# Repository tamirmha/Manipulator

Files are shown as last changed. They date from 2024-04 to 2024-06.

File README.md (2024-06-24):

# Homemade Manipulator Arm Project

Welcome to the Homemade Manipulator Arm project repository! This project features a DIY robotic arm with 6 degrees of freedom (6DoF) and a gripper. The arm is controlled using 4 MG1501 servos and 3 SG90 servos. The project includes SolidWorks 3D part designs, electrical schemas created with EasyEDA, and the ESP code for controlling the arm.
Use [PlatformIO](https://platformio.org/) in Visual Studio Code (VSCode) to manage and upload the code to the ESP microcontroller.

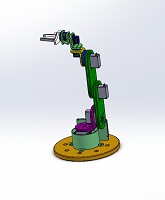
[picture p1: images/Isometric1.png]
Isometric View

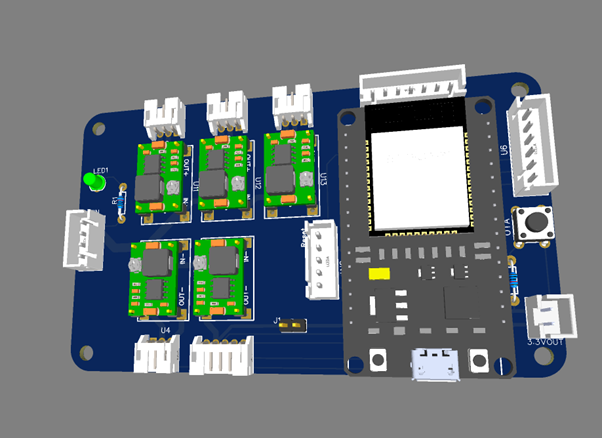
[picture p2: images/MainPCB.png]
Main PCB Board 3D

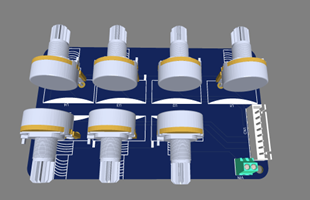
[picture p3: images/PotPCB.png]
Potentiometer PCB Board 3D

## Contents

- [Description](#description)
- [Components](#components)
- [Folder Structure](#folder-structure)
- [Usage](#usage)
- [Credits](#credits)
- [Sponsors](#sponsors)
- [License](#license)

## Description

This project is a homemade manipulator arm designed for educational purposes and hobbyist robotics enthusiasts. The arm is built using 3D-printed parts designed in SolidWorks and controlled using ESP32 microcontroller boards. The control methods include Bluetooth Low Energy (BLE) using the [RemoteXY](https://remotexy.com/) library or manual control using encoders (potentiometers).

The kinematics of the manipulator are represented using the Denavit-Hartenberg (DH) notation as follows:

| Link | a | α (deg) | d | θ (deg) |
|---|-----|---|---|---|
| 0 | 0 | 90 | 94.85 | 90 |
| 1 | 104 | 0 | 0 | 90 |
| 2 | 104 | 0 | 0 | 0 |
| 3 | 0 | 90 | -7.65 | 90 |
| 4 | 0 | -90 | 66.6  | 0 |
| 5 | 0 | 0 | 66.6  | 0 |

- `a_i`: Represents the link length along the \(x_i\) axis.
- `α_i`: Represents the twist angle about the \(x_i\) axis in degrees.
- `d_i`: Represents the link offset along the \(z_{i-1}\) axis.
- `θ_i`: Represents the joint angle about the \(z_{i-1}\) axis in degrees.

## Components

The manipulator arm features the following components:

- **Servos**:
  - 4 x [MG1501](https://www.pololu.com/file/0J729/HD-1501MG.pdf) servos (for joints)
  - 3 x [SG90 servos](http://www.ee.ic.ac.uk/pcheung/teaching/DE1_EE/stores/sg90_datasheet.pdf) (for gripper and the last wrists)
  
- **Electronics**:
  - ESP32 microcontroller board
  - PCB Board to control the robot
  - PCB Board with Potentiometers (for manual control using encoders)
  
- **3D Parts**:
  - Various parts designed in SolidWorks for the arm's structure
  
- **Electrical Schemas**:
  - Schemas created in EasyEDA for the wiring and electronic components layout
  - Full BOM can be found:
    <br>[For Manipulator](./schemas/Main%20Board/BOM_Manip.csv)
    <br>[For Potentiometers](./schemas/Potentiometer/BOM_Potensiometers.csv)
## Folder Structure

The repository is organized as follows:

/[Code](./Code/)
<br>&nbsp;&nbsp;&nbsp;&nbsp;├── [src/main.cpp](Code/src/main.cpp) &nbsp;&nbsp;&nbsp;# Main file of the Project
<br>&nbsp;&nbsp;&nbsp;&nbsp;├── [lib](Code/lib)&nbsp;&nbsp;&nbsp;&nbsp;&nbsp;&nbsp;&nbsp;&nbsp;&nbsp;&nbsp;&nbsp;&nbsp;&nbsp;&nbsp;&nbsp;&nbsp;&nbsp;&nbsp;&nbsp;&nbsp; # Folder containing help libraries
<br>/[Cad](./Cad/)
<br>&nbsp;&nbsp;&nbsp;&nbsp;├── [stl](./Cad/stl/)&nbsp;&nbsp;&nbsp;&nbsp;&nbsp;&nbsp;&nbsp;&nbsp;&nbsp;&nbsp;&nbsp;&nbsp; # Folder with stl files for 3D 
<br>&nbsp;&nbsp;&nbsp;&nbsp;├── *.sldprt &nbsp;&nbsp;&nbsp;&nbsp;# SolidWorks files 
printing
<br>/[Electrical_Schemas](./schemas/)
<br>&nbsp;&nbsp;&nbsp;&nbsp;    ├── [Main Board](./schemas/Main%20Board/)  &nbsp;&nbsp;&nbsp;&nbsp;&nbsp;&nbsp;&nbsp;&nbsp;&nbsp;&nbsp;&nbsp;&nbsp;&nbsp;&nbsp;&nbsp;&nbsp;&nbsp;&nbsp;&nbsp;   # Electrical schemas created in EasyEDA for the robot control PCB
<br>&nbsp;&nbsp;&nbsp;&nbsp;    ├── [Potentiometer Board](./schemas/Potentiometer/) &nbsp;&nbsp;&nbsp;&nbsp;  # Electrical schemas created in EasyEDA for the Potentiometer PCB
<br> /[docs](./docs/) &nbsp;&nbsp;&nbsp;&nbsp; # Datasheets for some of the components
<br> /[robodk](./robodk/) &nbsp;&nbsp;&nbsp;&nbsp; # Robodk station with the robot. Note: The movement of the manipulator in robodk is not exactly the same due to robodk mechanism build limitations.
<br>/README.md                             
## Usage

To replicate or modify this project, follow these steps:

1. **3D Printing**:
   - Print the 3D parts from the `\Cad\stl` directory using a 3D printer

2. **Assembly**:
   - Assemble the printed parts and servos according to the design

3. **Electronics**:
    <BR>Choose one of the following methods:
     - **Option 1: Order PCB Boards**:
       - Use the provided PCB design files (`*.zip`) in the repository's attachments to order custom PCB boards.
       <br>-  [Manipulator Main PCB](./schemas/Main%20Board/Gerber_Manip_PCB.zip)
       <br>- [Potentiometer PCB](./schemas/Potentiometer/Gerber_Potensiometers_PCB.zip)
     - **Option 2: Manual Wiring**:
       - Refer to the electrical schemas (`Electrical_Schemas`) and wire up the servos, microcontroller, and other components manually based on the schematic PDFs (`*.pdf`).
       <br>-  [Manipulator Main Scheme](./schemas/Main%20Board/Schematic_Manip.pdf)
       <br>- [Potentiometer Scheme](./schemas/Potentiometer/Schematic_Potensiometers.pdf)

4. **Programming**:
   - Use PlatformIO in Visual Studio Code (VSCode) to manage and upload the code

5. **Control**:
   - Use the RemoteXY library for BLE control, or wire up potentiometers for manual control

## Credits

This project was created by Tamir Mhabary. Feel free to contribute by submitting pull requests or reporting issues.

## Sponsors
This project is proudly sponsored by [PCBWay](https://pcbway.com/g/lxAijI).\
[PCBWay](https://pcbway.com/g/lxAijI)  provided the manufacturing of the PCB boards and 3D printing services for this project. 

[PCBWay](https://pcbway.com/g/lxAijI)  is a one-stop solution for PCB prototyping, manufacturing, and assembly, as well as 3D printing services. Their high-quality products and excellent customer service make them a top choice for electronics enthusiasts and professionals alike.\
Visit [PCBWay](https://pcbway.com/g/lxAijI) for more information on their services and to get started on your own projects!

<a href="https://www.pcbway.com/project/shareproject/Manipulator_PCB_435606e7.html">PCB from PCBWay</a>

## License

This project is licensed under the [MIT License](LICENSE). Feel free to use, modify, or distribute this code and design for personal or educational purposes.

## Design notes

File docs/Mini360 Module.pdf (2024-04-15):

GroundStudio® Mini360 module Datasheet

# Groundstudio Mini360 module

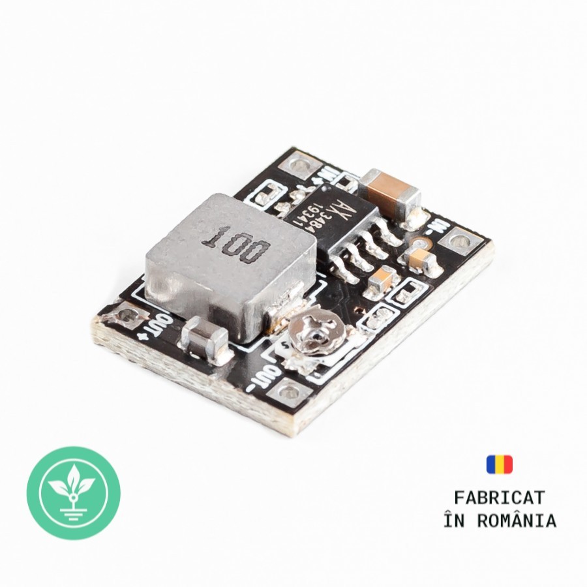
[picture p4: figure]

## Table of Contents

## Module Circuit Schematic

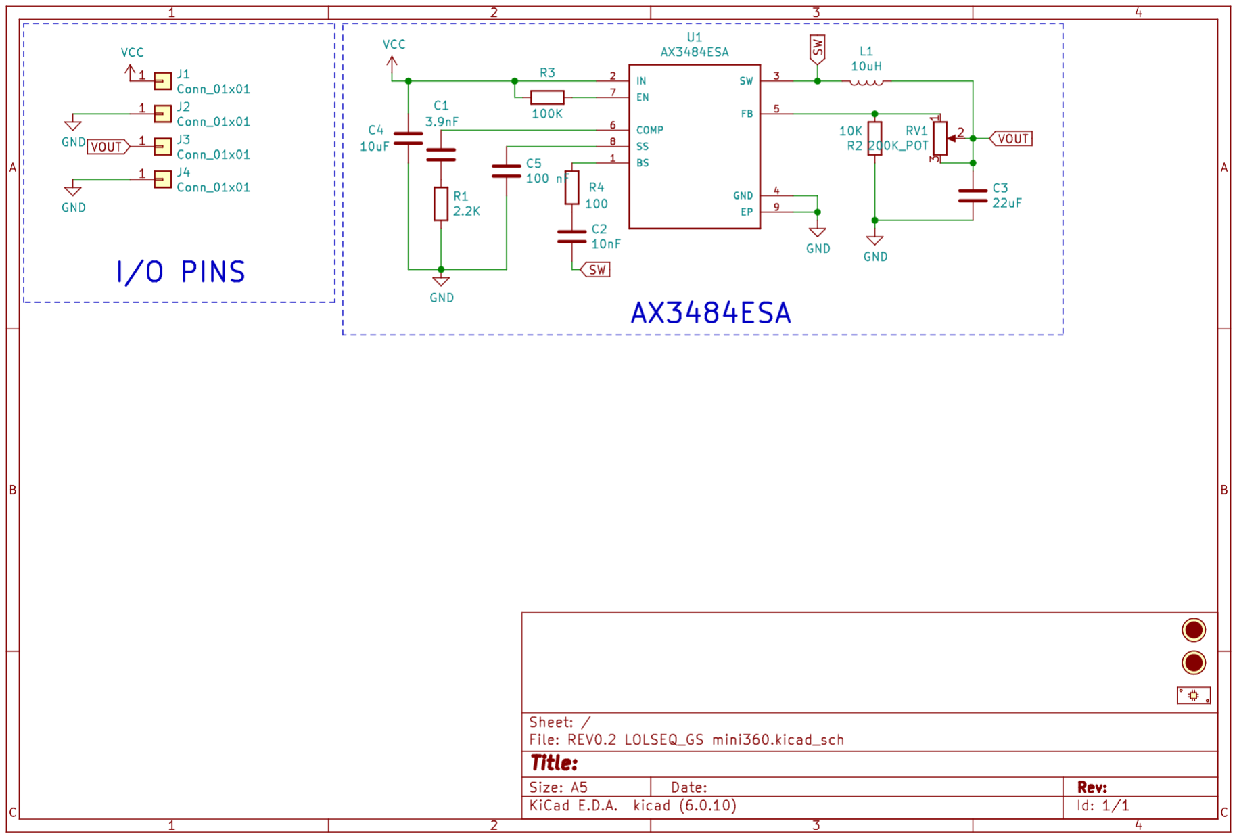
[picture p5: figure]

Figure 2: GroundStudio Mini360 module schematic circuit [Revision 0.0.2]

## Open Source

This is an Open Source project, you can find all the technical documents online: https://github.com/GroundStudio/GroundStudio_Mini360_module

## License

All documentation for GroundStudio Marble Pico is released under the Attribution-ShareAlike 4.0 International (CC BY-SA 4.0) (https://creativecommons.org/licenses/by-sa/4.0/) license. You are welcome to use this for commercial purposes.
Please consider contributing back to this project or others to help the open-source hardware community continue to thrive and grow!

## Overview

This product represents a step-down voltage source that can be used in various projects that use a small space where you need to transform a voltage between 4.75V-23V into one of a lower level in the range of 0.925V to 20V with a consumption of current up to 3A.
Super compact and capable, this Buck DC-DC converter can lower the voltage with an efficiency of up to 95%, having an adjustable output voltage, which can be adjusted using the onboard potentiometer. The output voltage will always be lower than the input voltage.
NOTE - The product needs adequate cooling depending on the level of the current. If the cooling is not properly ensured, it will fail.
For cooling, you need to attach a radiator (not included) and ensure a proper air flow: the case must be ventilated or use a fan (not included).

## Technical specifications

Vin: from 4.75V to 23V;
Vout: from 0.925V to 20V;
Maximum current: 3A;
Frequency: 350kHz;
PCB dimensions: 17.7mm x 12.7mm

## Legal disclaimer notice

This development board is considered a subassembly in accordance with FCC CFR Title 47 §15.101(e):
https://www.ecfr.gov/current/title-47/chapter-I/subchapter-A/part-15/subpart-B/section-15.101#p-15.101(e) (https://www.ecfr.gov/current/title-47/chapter-I/subchapter-A/part-15/subpart-B/section-15.101)
The device does not have a standalone functionality and does not include an enclosure or power supply.
The device is mainly intended for development and prototyping but it can be integrated into a product. In this case it is the responsibility of the developer/manufacturer to obtain all the necessary certifications.
GroundStudio is a registered trademark of ARDUSHOP SRL: https://www.tmdn.org/tmview/#/tmview/detail/EM500000018364087

## Developer info

ARDUSHOP SRL
Addr: Str. Aleea Unirii, Nr. 8, Ap. 7, Loc. Selimbar, Jud. Sibiu, ROMANIA, 557260 e-mail: office@ardushop.ro

## Datasheet Revision History

[Revision 1] - Initial version release

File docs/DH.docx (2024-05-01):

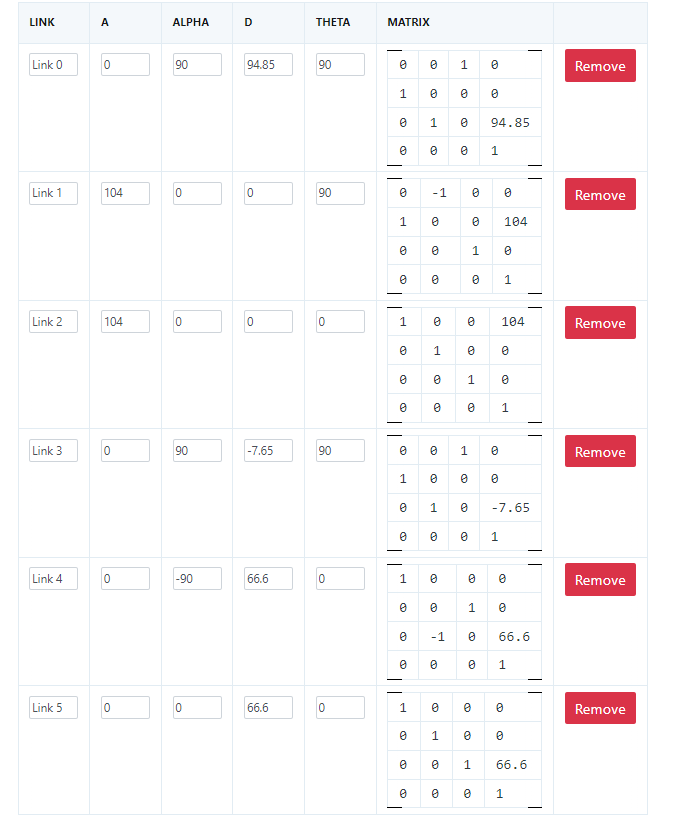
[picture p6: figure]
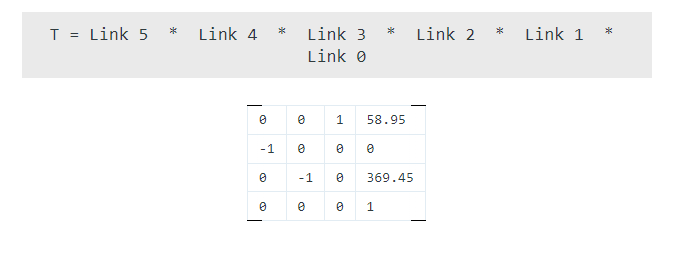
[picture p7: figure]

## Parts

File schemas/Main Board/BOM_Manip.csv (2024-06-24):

ID | Name | Footprint | Quantity
1 | ESP32 (DEVKITV1) | ESP32-DEVKITV1_ESP32-DEVKITV1 | 1
2 | B2B-XH-A-M | CONN-TH_B2B-XH-A-M | 1
3 | B5B-XH-A (LF)(SN) | CONN-TH_B5B-XH-A-LF-SN | 1
4 | HDR-M-2.54_1x2 | HDR-M-2.54_1X2 | 1
5 | LED-TH-3mm_G | LED-TH_BD3.0_GREEN | 1
6 | TS02-66-55-BK-160-LCR-D | SW-TH_4P-L6.0-W6.0-P4.50-LS6.5 | 1
7 | B7B-XH-A | CONN-TH_7P-P2.50_B7B-XH-A-LF-SN | 1
8 | 10K | R_AXIAL-0.3 | 1
9 | 12V500ohm 24V1K | R_AXIAL-0.3 | 1
10 | S3B-PH-K-S-(LF)(SN) | CONN-TH_3P-P2.00_S3B-PH-K-S-LF-SN | 4
11 | S5B-PH-K-S-(LF)(SN) | CONN-TH_S5B-PH-K-S-LF-SN | 1
12 | B6B-XH-A(LF)(SN) | CONN-TH_6P-P2.50_B6B-XH-A-LF-SN | 1
13 | Mini360 3A Module | MINI360 BUCK CONVERTER | 5
14 | B4B-XH-AM(LF)(SN) | CONN-TH_B4B-XH-AM-LF-SN | 1

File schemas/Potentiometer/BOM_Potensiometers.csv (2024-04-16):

ID | Name | Designator | Footprint | Quantity | Manufacturer Part | Manufacturer | Supplier | Supplier Part
1 | B8B-XH-A (LF)(SN) | CN1 | CONN-TH_B8B-XH-A-LF-SN | 1 | B8B-XH-A(LF)(SN) | JST | LCSC | C157972
2 | WH148 | U2,U3,U4,U5,U6,U7,U1 | WH148 | 7 |  |  | ANDREA
3 | 282834-2 | VIN | CONN-TH_2P-P2.54_282834-2 | 1 | 282834-2 | TE Connectivity(泰科电子) | LCSC | C592983

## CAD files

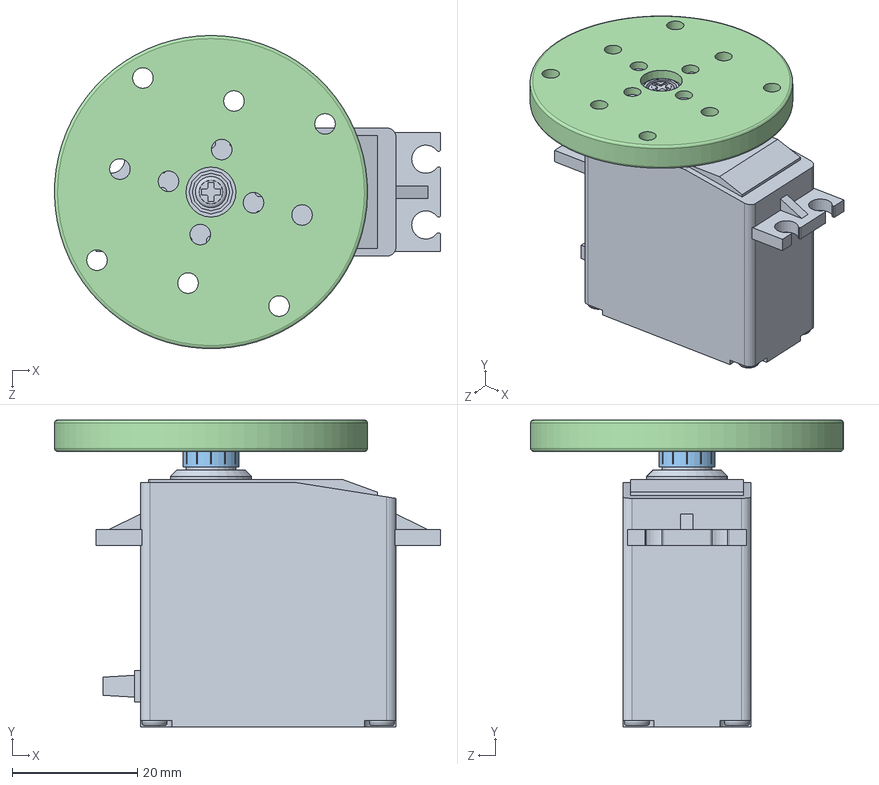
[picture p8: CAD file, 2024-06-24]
Cad/1501MG_adapter.SLDASM
61.6 x 49.0 x 50.0 mm
ServoHD1501MG
Servo Output Shaft
ServoHD1501MG_horn
base

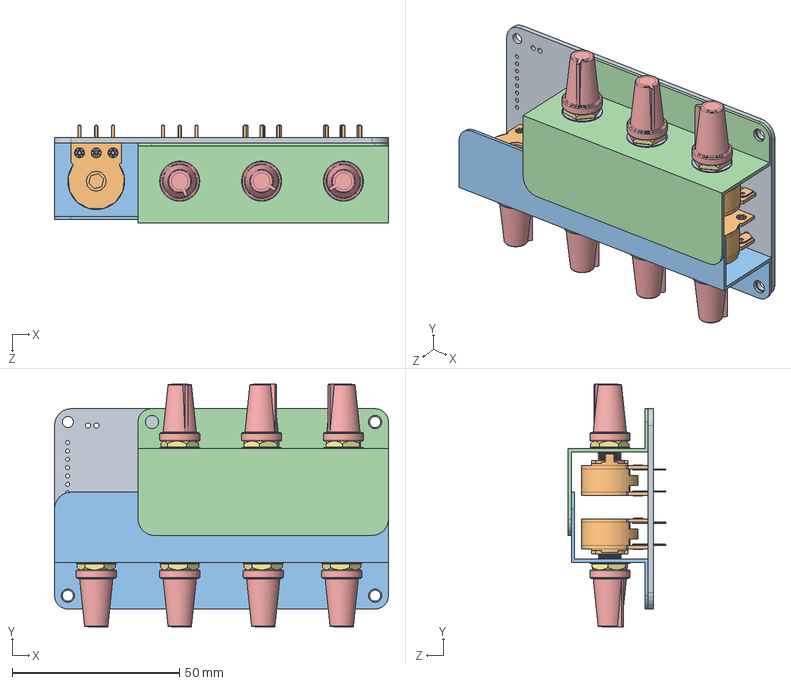
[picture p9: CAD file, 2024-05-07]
Cad/Potentaiometer/Main_assem.SLDASM
100.0 x 72.7 x 29.3 mm
Baord
potenciometro x 7
Cover
Cover_small
perilla x 7
rondana x 7
tuerca x 7

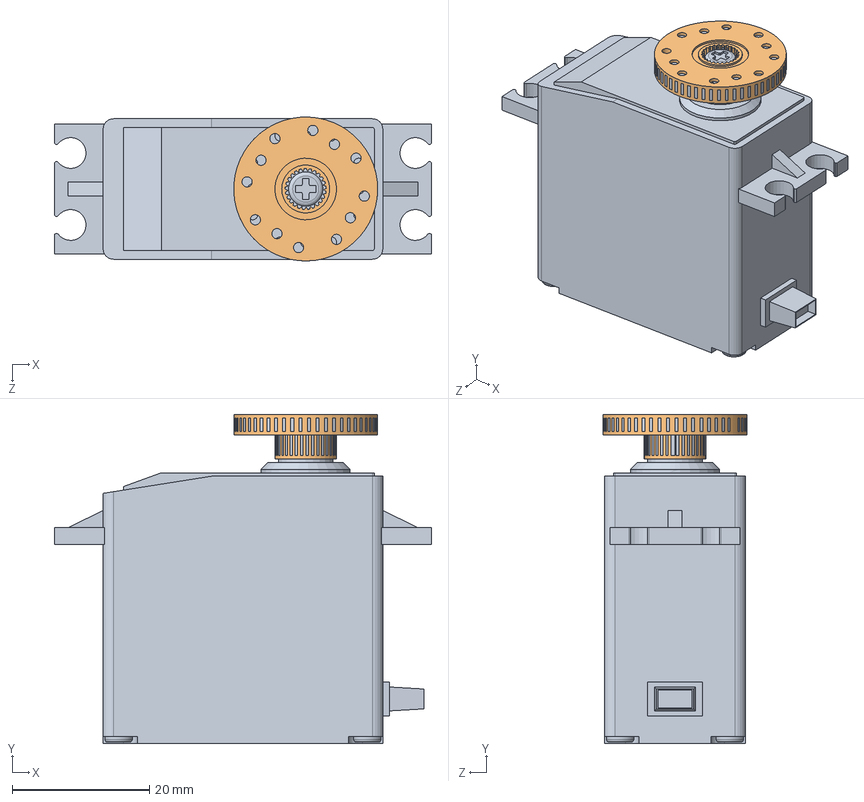
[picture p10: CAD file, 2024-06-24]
Cad/1501MG_assem.SLDASM
55.0 x 48.0 x 21.0 mm
ServoHD1501MG
ServoHD1501MG_horn

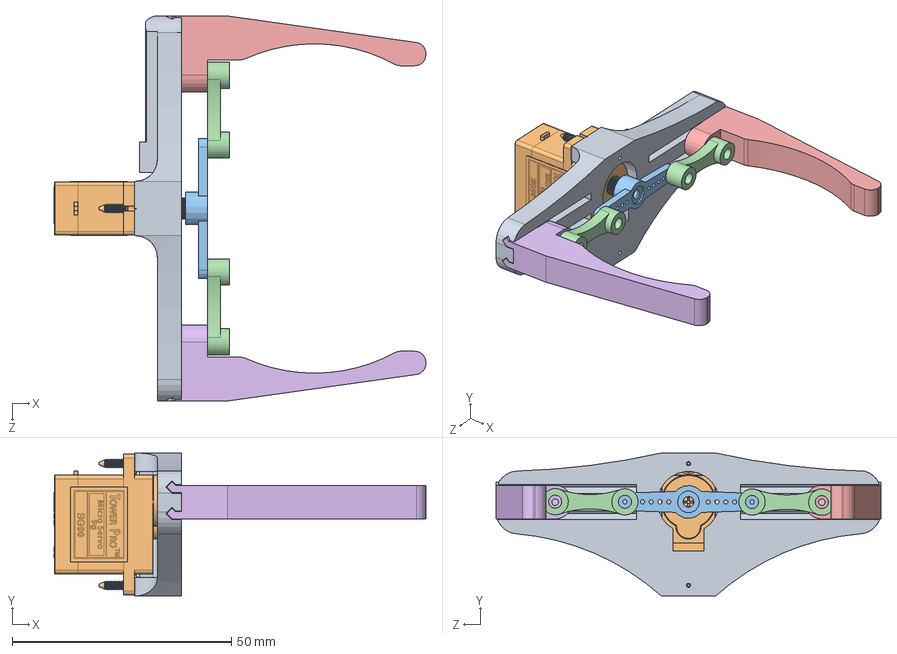
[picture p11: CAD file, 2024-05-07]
Cad/Linear Gripper.SLDASM
84.8 x 32.6 x 87.8 mm
Linear Base
SG90 - Micro Servo 9g - Tower Pro
Horn
gripper_linear_link x 2
gripper_grip
Mirrorgripper_grip

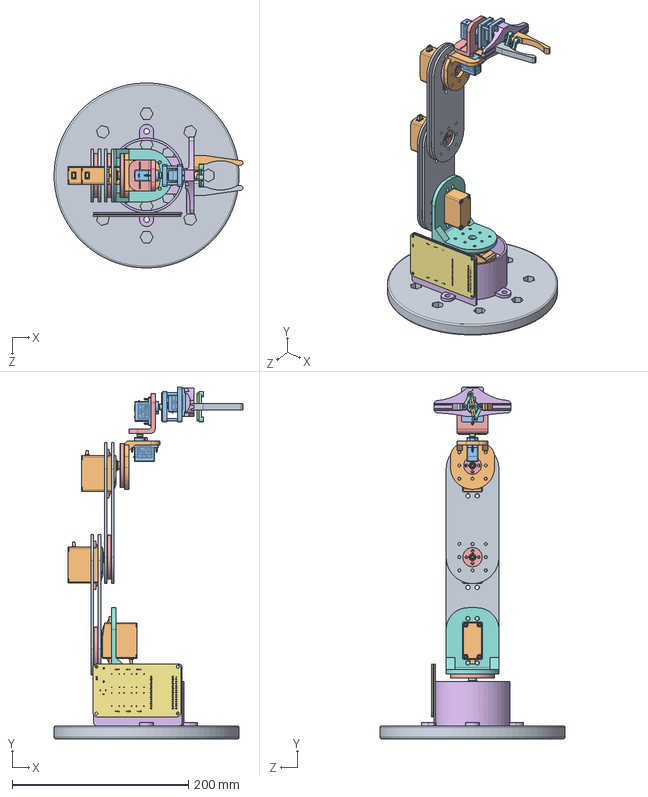
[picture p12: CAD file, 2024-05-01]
Cad/main.SLDASM
214.3 x 399.5 x 209.9 mm
robot_base
ServoHD1501MG x 4
ServoHD1501MG_horn x 4
base x 4
base_round
OBJ_PCB_Manip
link_90
link x 4
link_90_small
SG90 - Micro Servo 9g - Tower Pro x 3
SG90 - Micro Servo 9g - Tower Pro.3 x 2
link_90_small_short
Linear Base
Horn
gripper_linear_link x 2
gripper_grip
Mirrorgripper_grip
ee_link

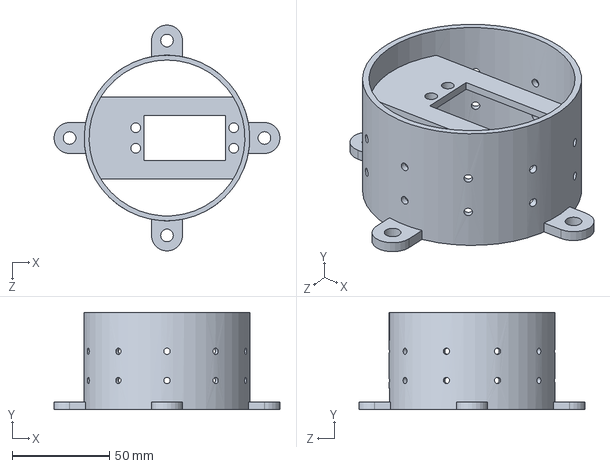
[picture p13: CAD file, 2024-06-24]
Cad/base_round.SLDPRT
116.0 x 50.0 x 116.0 mm

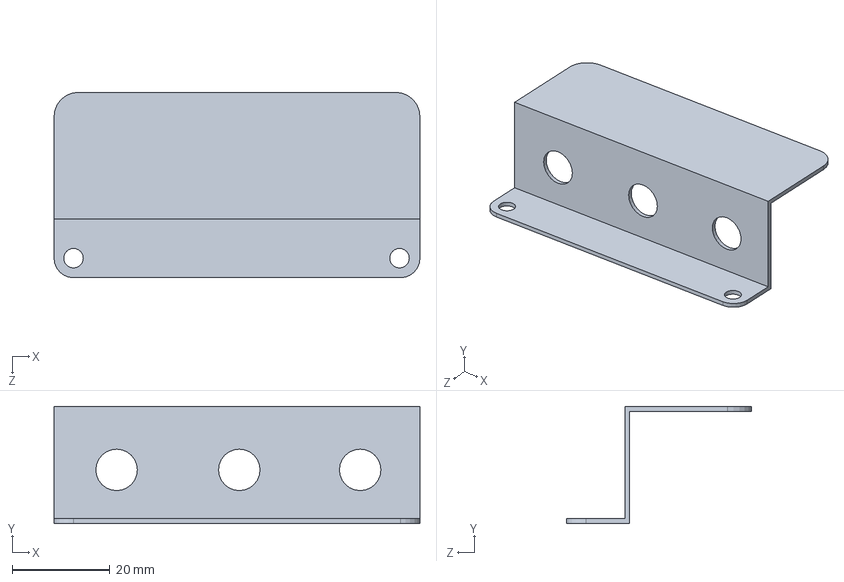
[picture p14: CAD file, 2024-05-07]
Cad/Potentaiometer/Cover_small.SLDPRT
75.0 x 24.0 x 38.0 mm

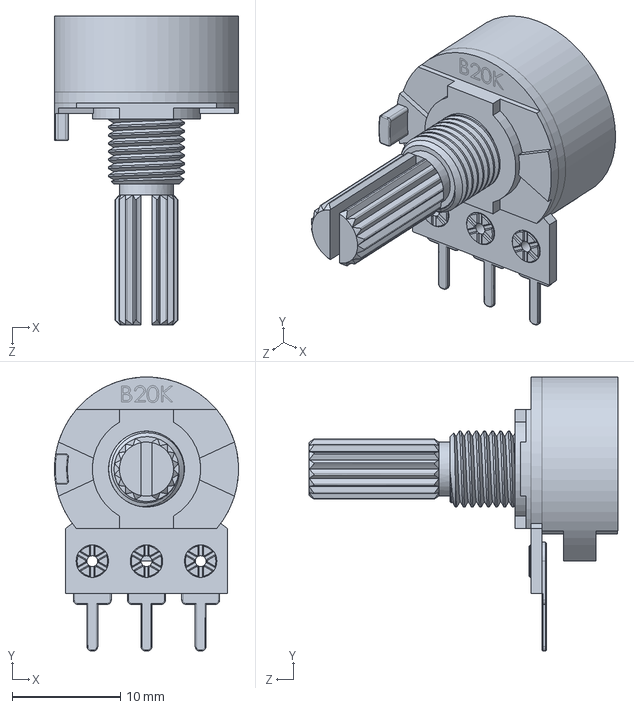
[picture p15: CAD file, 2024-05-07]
Cad/Potentaiometer/potenciometro-5.snapshot.2/potenciometro.SLDPRT
17.0 x 25.3 x 28.5 mm

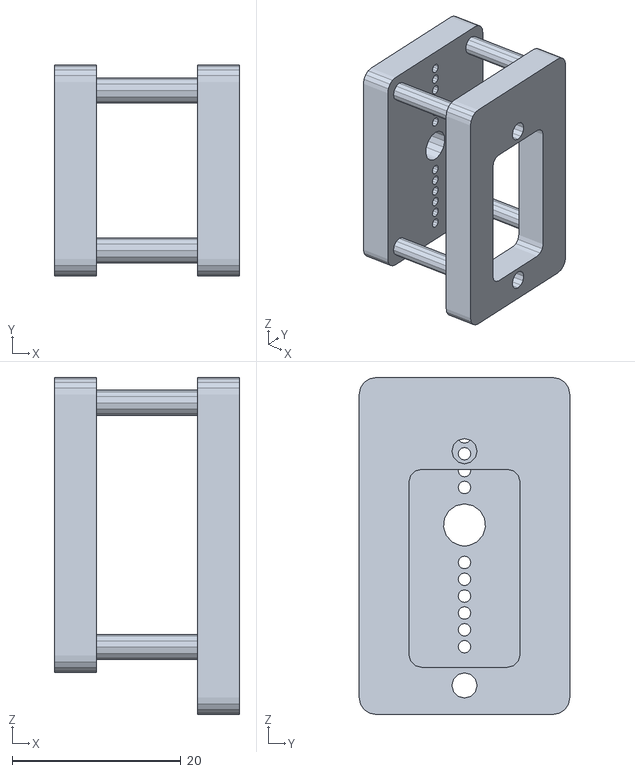
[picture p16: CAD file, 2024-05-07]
Cad/stl/gripper/ee_link.STL
22.0 x 25.0 x 40.0

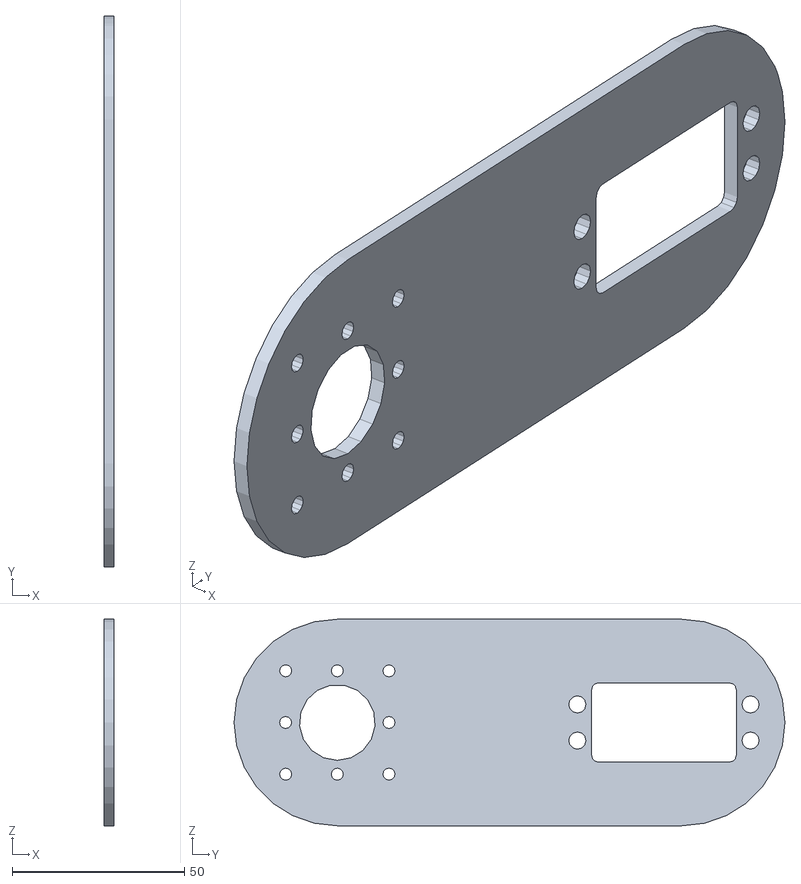
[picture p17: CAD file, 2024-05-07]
Cad/stl/linkX4.STL
3.00 x 160.0 x 60.0

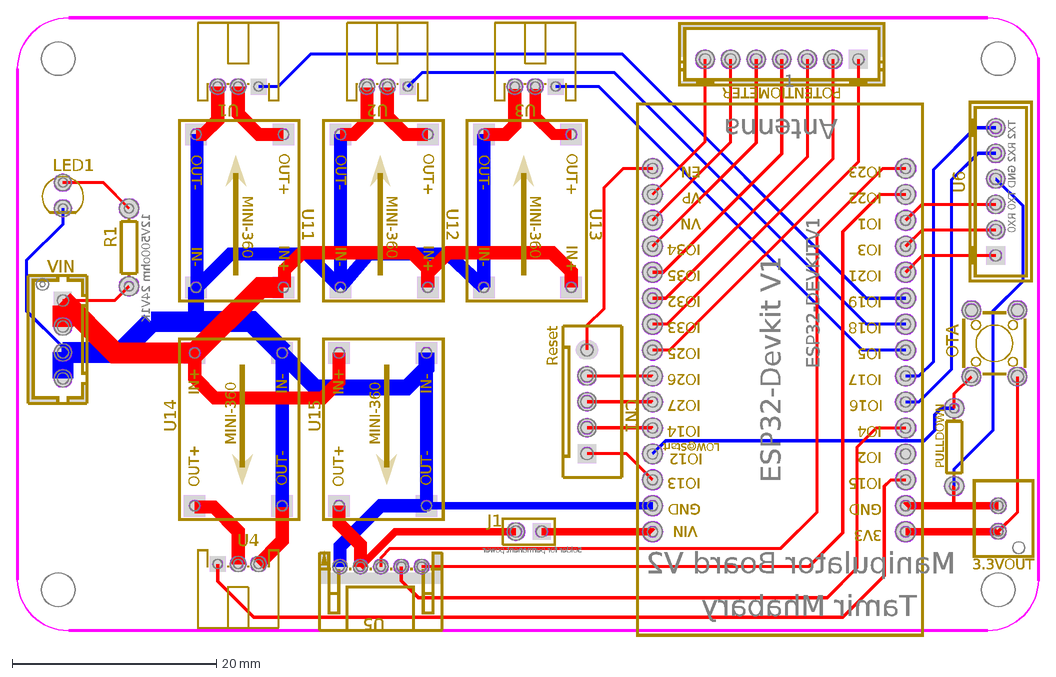
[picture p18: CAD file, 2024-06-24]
schemas/Main Board/PCB_Manip_2024-06-24.dxf
Manipulator Board V2
Tamir Mhabary
Solder for permanent power
TX2 RX2 GND TX0 RX0
Reset
LOW@Start
U6
POTENTIOMETER
PULLDOWN
OTA
CN1
J1
LED1
1
ESP32-DEVKITV1
3V3
GND
IO15
IO2
IO4
IO16
IO17
IO5
IO18
IO19
IO21
IO3
IO1
IO22
IO23
VIN
IO13
IO12
IO14
IO27
IO26
IO25
IO33
IO32
IO35
IO34
VN
VP
EN
ESP32-Devkit V1
Antenna
3.3VOUT
12V500ohm 24V1K
R1
U1
U2
U3
U4
U5
U11
MINI-360
IN-
IN+
OUT-
OUT+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

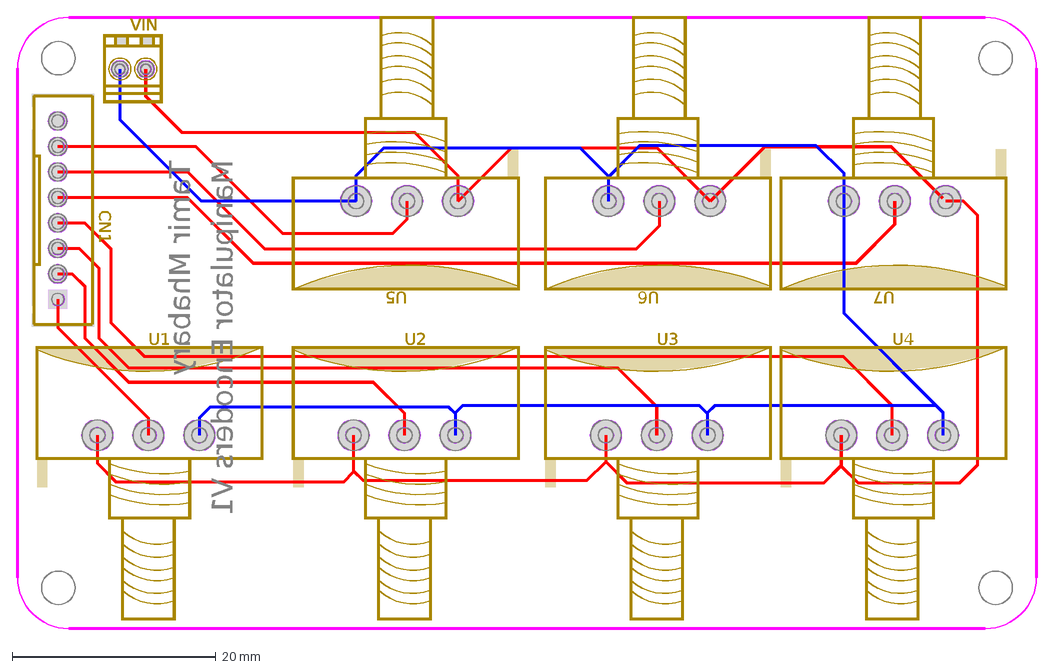
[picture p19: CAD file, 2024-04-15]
schemas/Potentiometer/PCB_Potensiometers_2024-04-15.dxf
Manipulator Encoders V1
Tamir Mhabary
CN1
U2
U3
U4
U5
U6
U7
VIN
U1

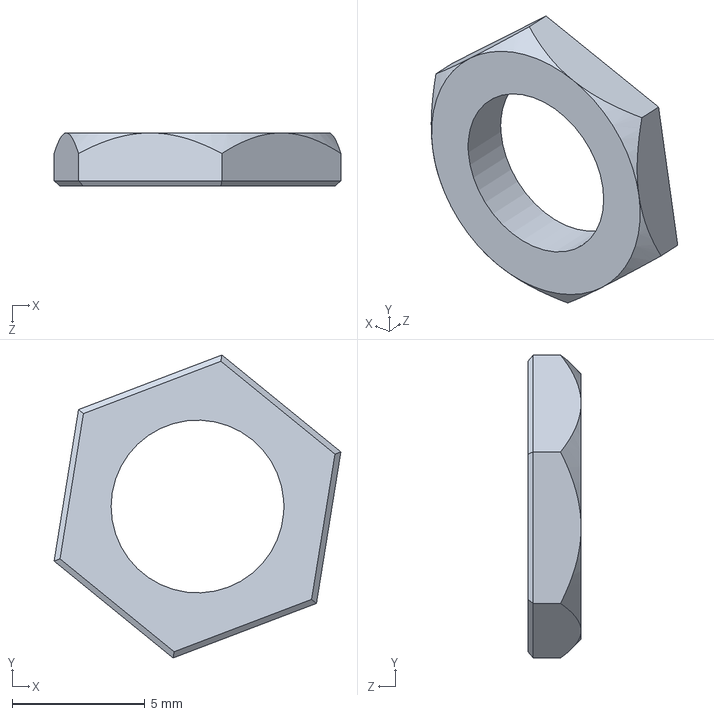
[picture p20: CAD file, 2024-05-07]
Cad/Potentaiometer/potenciometro-5.snapshot.2/tuerca.SLDPRT
10.8 x 11.4 x 2.00 mm

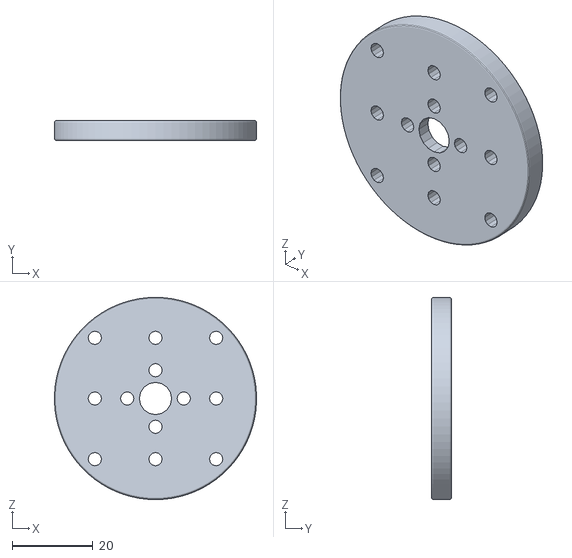
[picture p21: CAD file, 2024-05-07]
Cad/stl/baseX4.STL
50.0 x 5.00 x 50.0

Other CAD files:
Cad/stl/Potentiometer/Cover_small.STL
Cad/stl/gripper/gripper_linear_linkX2.STL
Cad/stl/Potentiometer/Cover.STL
Cad/pcbHOlder.SLDPRT
Cad/Horn.SLDPRT
Cad/Linear Base.SLDPRT
Cad/Mirrorgripper_grip.SLDPRT
Cad/OBJ_PCB_Manip.SLDPRT
Cad/Potentaiometer/Baord.SLDPRT
Cad/Potentaiometer/Cover.SLDPRT
Cad/Potentaiometer/potenciometro-5.snapshot.2/perilla.SLDPRT
Cad/Potentaiometer/potenciometro-5.snapshot.2/rondana.SLDPRT
Cad/PowerHD1501MG_STEP.stp
Cad/SG90 - Micro Servo 9g - Tower Pro.3.SLDPRT
Cad/SG90 - Micro Servo 9g - Tower Pro.SLDPRT
Cad/Servo Micro.SLDPRT
Cad/Servo Output Shaft.SLDPRT
Cad/ServoHD1501MG.SLDPRT
Cad/ServoHD1501MG_horn.SLDPRT
Cad/base.SLDPRT
Cad/ee_link.SLDPRT
Cad/gripper_grip.SLDPRT
Cad/gripper_linear_link.SLDPRT
Cad/link.SLDPRT
Cad/link_90.SLDPRT
Cad/link_90_small.SLDPRT
Cad/link_90_small_short.SLDPRT
Cad/robot_base.SLDPRT
Cad/stl/base_round.STL
Cad/stl/gripper/Linear Base.STL
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

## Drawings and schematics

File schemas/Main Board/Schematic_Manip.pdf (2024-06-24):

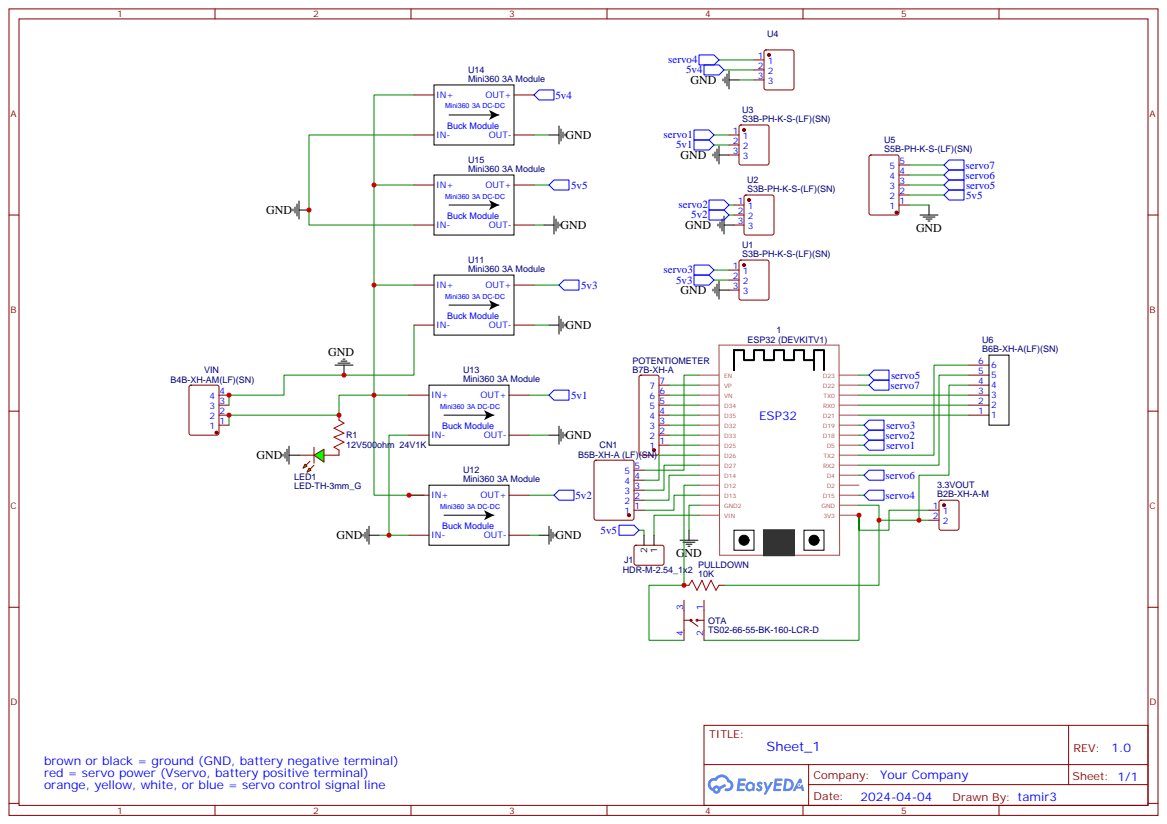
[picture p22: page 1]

VIN

brown or black = ground (GND, battery negative terminal)
red = servo power (Vservo, battery positive terminal)
orange, yellow, white, or blue = servo control signal line

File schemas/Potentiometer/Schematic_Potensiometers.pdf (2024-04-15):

# GNDVin

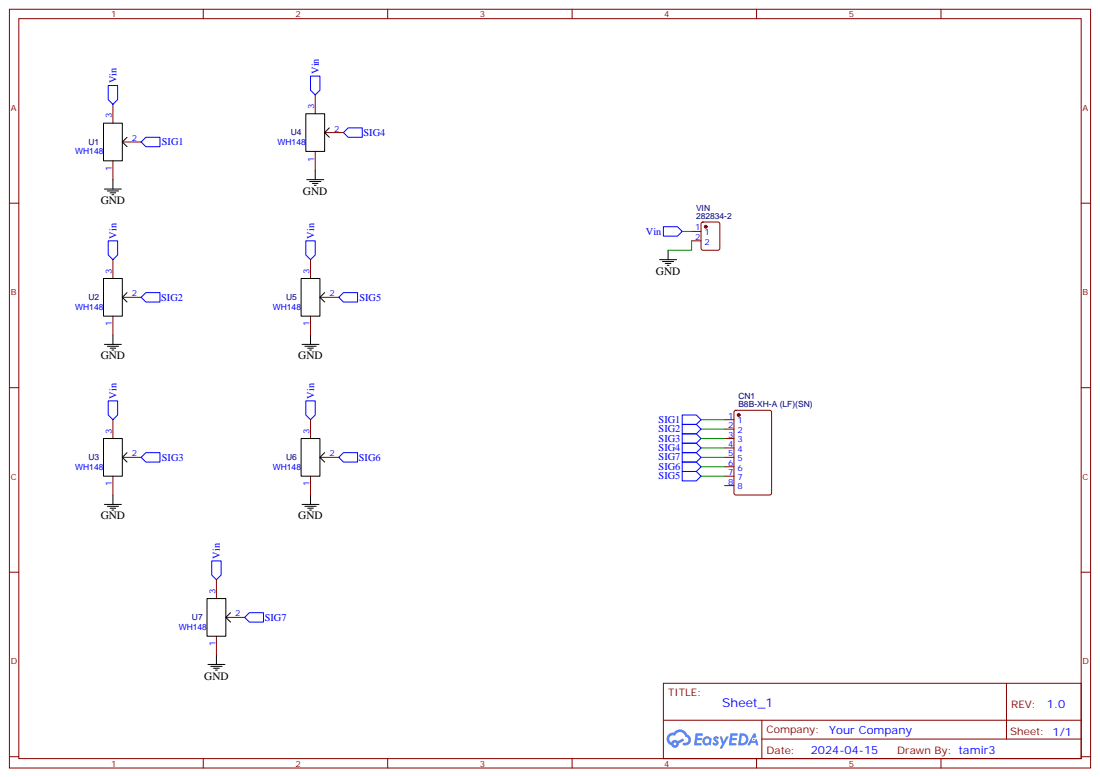
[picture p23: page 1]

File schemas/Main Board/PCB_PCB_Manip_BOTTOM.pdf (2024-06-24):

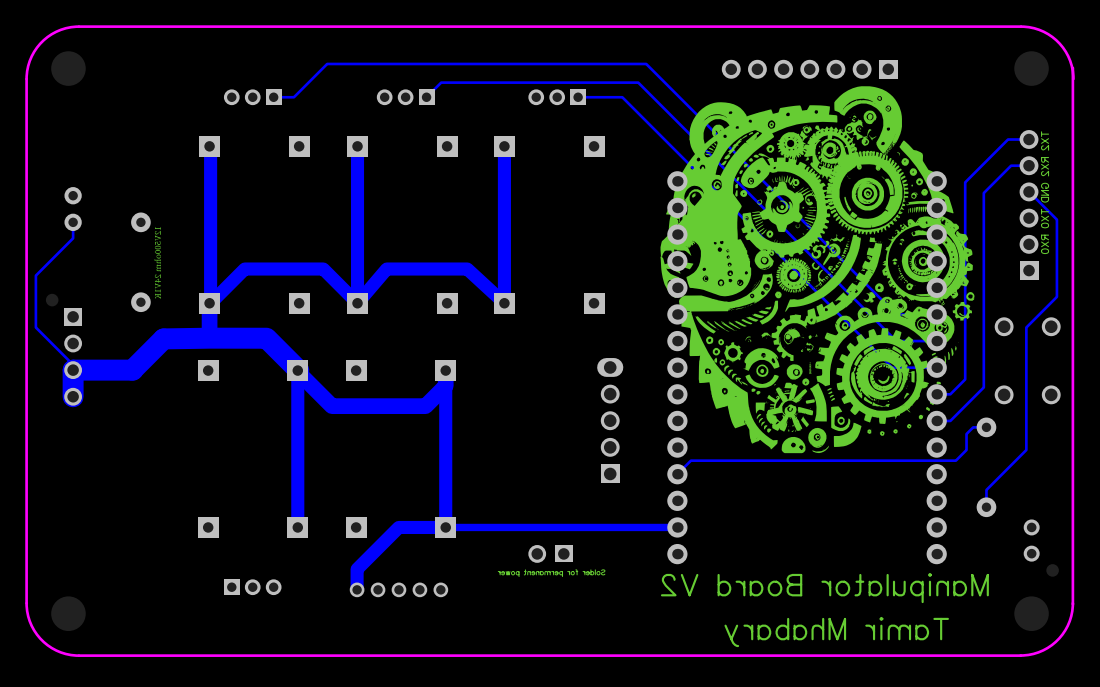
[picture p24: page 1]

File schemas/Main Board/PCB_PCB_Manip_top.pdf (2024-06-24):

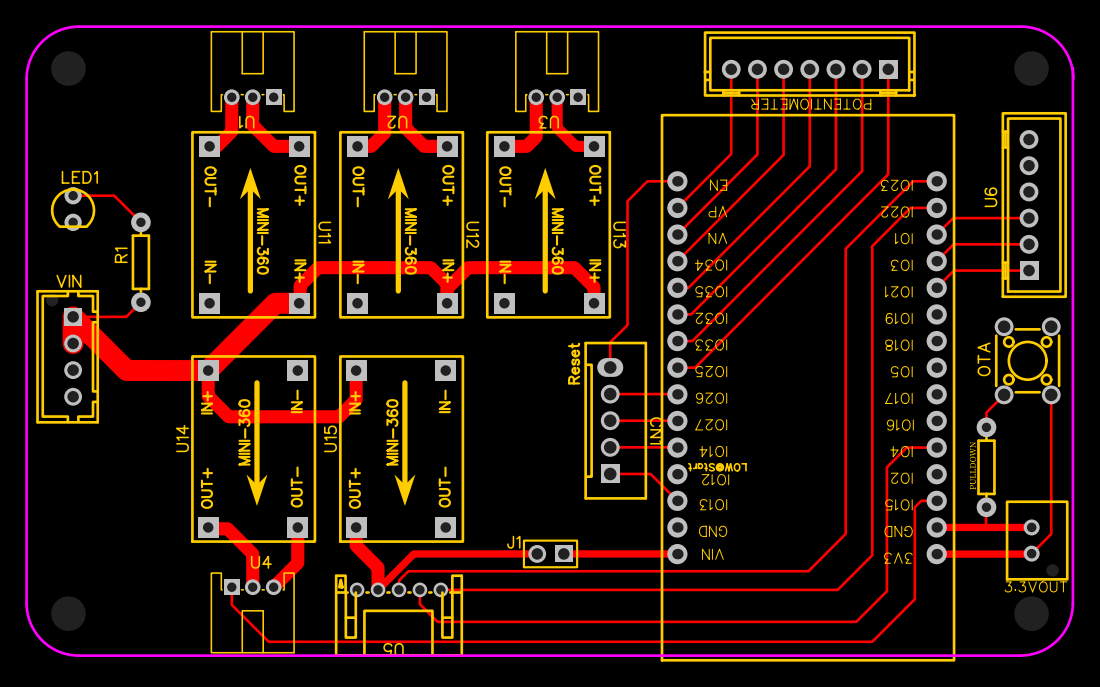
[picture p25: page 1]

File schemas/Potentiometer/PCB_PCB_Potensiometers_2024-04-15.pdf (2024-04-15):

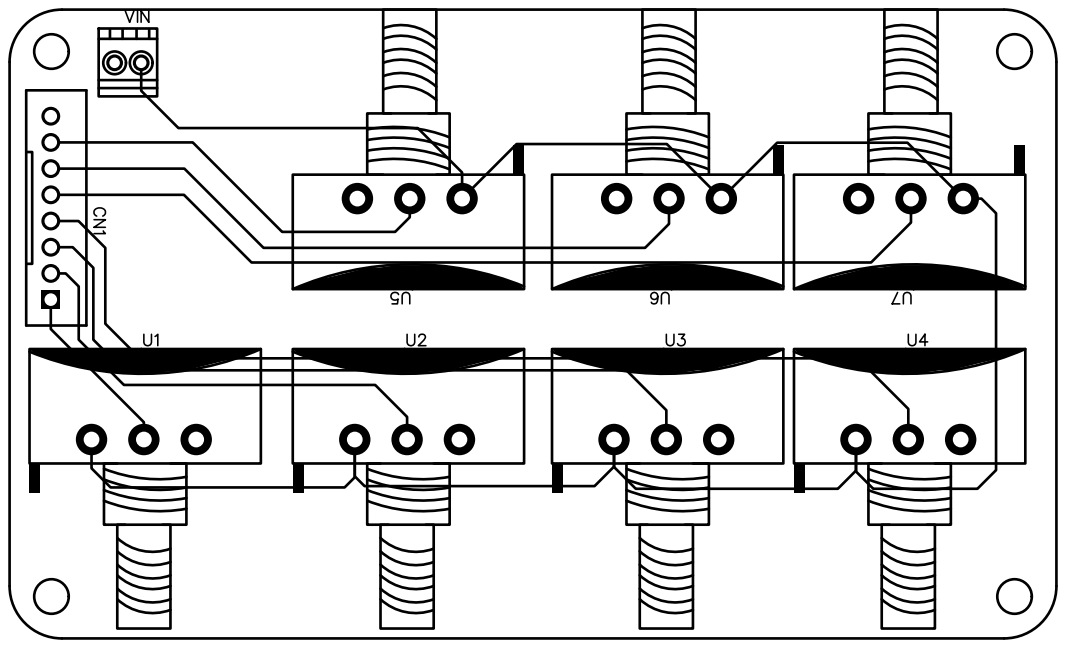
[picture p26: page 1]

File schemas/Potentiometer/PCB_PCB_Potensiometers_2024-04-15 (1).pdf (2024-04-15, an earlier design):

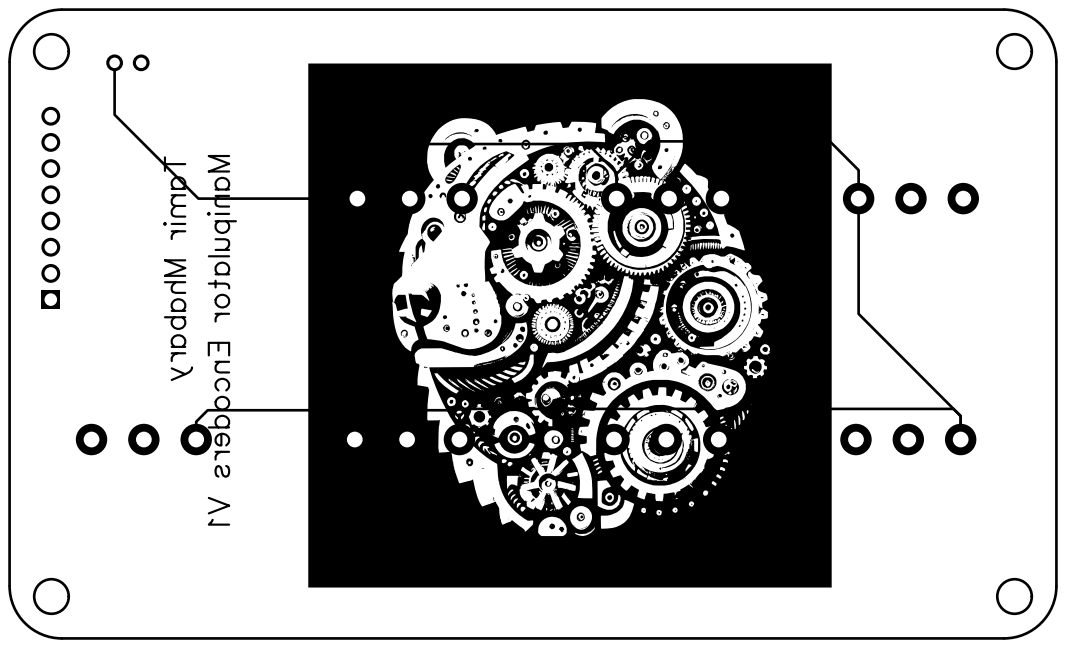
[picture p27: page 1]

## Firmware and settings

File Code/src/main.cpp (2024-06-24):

#include <Arduino.h>
#include <decode_packet.h>
#include <encoder.h>
#include <Kinematic.h>
#include <my_remotexy.h>
#include <ota.h>
#define LED 2

void setup() {
    Serial.begin(115200);
    Serial.println("Start Program");
    setup_servo();
    encoder_setup();
    setup_ota();
    // remotexy_setup();
    for(int i=0; i < NUM_MOTORS; i++)  servo_control(45, i); 
    RobotArm arm = setup_kin();
    use_example(arm);
    pinMode(LED,OUTPUT);
}


void loop() {

    serial_listener();
    loop_ota();

    // remotexy_loop();
    // if (RemoteXY.connect_flag)
    // {   
    //   servo_control(remotexy2angle(RemoteXY.Base), 0);
    //   servo_control(remotexy2angle(RemoteXY.Shoulder), 1);
    //   servo_control(remotexy2angle(RemoteXY.wrist1), 2);
    //   servo_control(remotexy2angle(RemoteXY.wrist2), 3);
    //   servo_control(remotexy2angle(RemoteXY.wrist3), 4);
    //   servo_control(remotexy2angle(RemoteXY.Base), 5);
    //   if (RemoteXY.Gripper)
    //     servo_control(0, 6);
    //   else
    //     servo_control(SERVO_MAX_DEGREE, 6);
    // }
    // else  // Encoders control the motors
    // {
      std::array<int, NUM_MOTORS> angles = encoder_loop();
      for(int i=0; i < NUM_MOTORS; i++)   servo_control(angles[i], i);   // 
    // }
    digitalWrite(LED,HIGH);
    delay(50);
    digitalWrite(LED,LOW);
    delay(50);
}

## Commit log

2024-04-15 add electrical schemas
    [PCB_Manip_2024-04-15.dxf, PCB_Potensiometers_2024-04-15.dxf]
2024-04-15 add CAD files
    [1501MG_adapter.SLDASM, 1501MG_assem.SLDASM, Horn.SLDPRT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]
2024-04-16 Add: BOM
    [BOM_Manip.csv, BOM_Potensiometers.csv]
2024-05-01 Update: CAD Add: RoboDK Add: DH Notation data
    [1501MG_adapter.SLDASM, 1501MG_assem.SLDASM, Linear Base.SLDPRT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]
2024-05-01 Update: readme
    [main.SLDASM]
2024-05-07 Update: Cad Files
    [1501MG_adapter.SLDASM, 1501MG_assem.SLDASM, Baord.SLDPRT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]
2024-06-24 Change: cad files updated
    [1501MG_adapter.SLDASM, 1501MG_assem.SLDASM, Linear Base.STL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]
2024-06-24 Fix: PCB BOARD- add OTA OPTION, jumper to power the esp and more minor fixes
    [BOM_Manip.csv, PCB_Manip_2024-04-15.dxf, PCB_Manip_2024-06-24.dxf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]
2024-06-24 (CODE) Change: Potentiometer pins Add: OTA OPTION Add: Kinematic solver ( Didn't finish) Disable: RemotyXY - not enough space at esp with OTA
    [main.cpp]
2024-06-24 Update: Readme - add link to order from PCBWAY
